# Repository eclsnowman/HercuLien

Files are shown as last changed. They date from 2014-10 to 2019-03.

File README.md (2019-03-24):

HercuLien
=========

HercuLien - Large Format, Dual Extrusion, Bowden/Direct Drive Modular, 3D Printer. Inspired by many... Created by me.

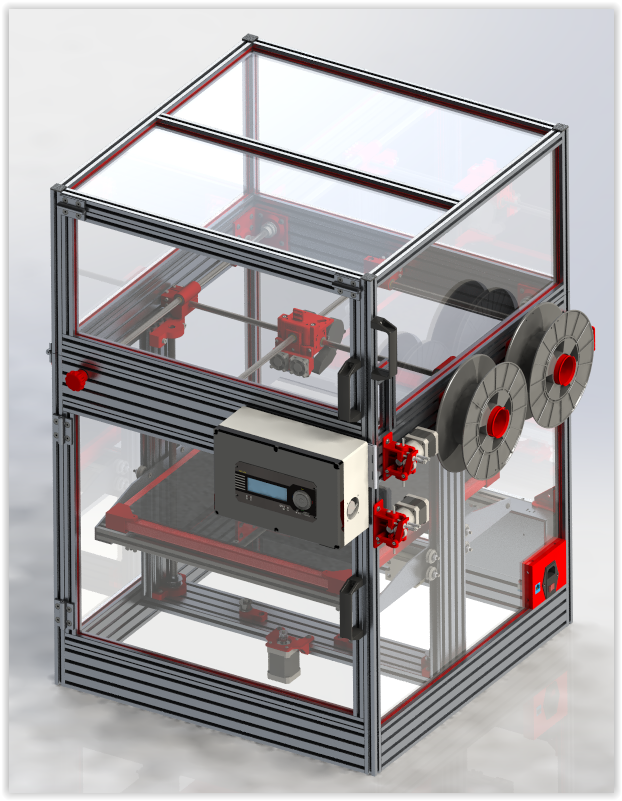
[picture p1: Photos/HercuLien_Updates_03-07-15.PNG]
HercuLien 3D Printer Render Image


This printer is the culmination of what I have learned so far since I started in 3D printing. My journey began when a friend of mine built a Prusa i3. The first time I saw his printer running I was hooked and knew I had to build one. But I was not happy with the 8"8"8" build volume of the i3. I wanted to design something bigger. At that time I had no 3D modeling experience. I figured it would be good training to learn Solidworks and design my own printer, that way once I actually built one I would have the skills to put it to use. My first attempt was my CoreXY design which is also uploaded to github. There were many things I liked about that printer, but speed and consistent print dimensions were not included in that list. 

While I was fighting with my CoreXY design I started following Tim Rastall on Google Plus. I really liked his Ingentus design, but I liked the idea of belts over spectra line. Then Jason Smith released his Eustathios designs which was a variant of of Ingentus using belts and lead screws. I knew I wanted that printer. But he released the files in sketchup. I really liked solidworks which was the software I was teaching myself during my design process. So I remodeled the Eustathios, made some changes, and eventually built the printer. The printer worked amazing. It was so much faster than my CoreY, printed part dimensions were spot on, and bowden extruders were not the nightmare I thought they would be listening to others online. In fact I designed a new extruder based on the airtripper design that allowed me to tune retraction perfectly. It is to the point that I don't think a direct drive extruder could do any better.

Once I had Eustathios up and running so well I wanted to change my CoreY to something similar. I used the aluminum frame from the CoreXY and my z-axis design which had always performed perfectly. Then I redesigned the rest from scratch. I have been running this new design for several months. I call it HercuLien (due to it's size and my last name). It is an amazing printer. I can print at very high speeds. It has a large build volume, dual extrusion, and is easily enclosed for trouble free abs printing. If you build one I hope you enjoy it as much as I have. I also hope this can act as a jumping off point for someone else to build and even better printer.

Now that Google+ has died, the Community around the HercuLien printer and the Eustathios printer have moved to: https://forum.makerforums.info/c/herculien . This is thanks in great part to Michael K Johnson, who worked his magic to retain the years of great community interaction on G+ and ported it into the Discourse community over on Makerforums. If you are looking for support or community interaction on these printers moving forward, this is the place to go.

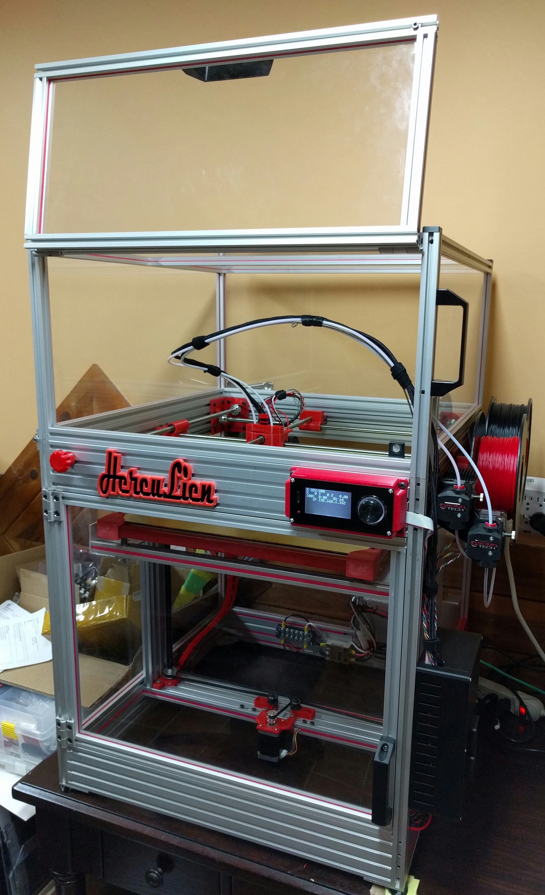
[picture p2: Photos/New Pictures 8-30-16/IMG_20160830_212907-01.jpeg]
Photo of HercuLien

(Photo of HercuLien with recent update to Azteeg X5 GT dual extruder smoothieware printer controller and Viki2 LCD)

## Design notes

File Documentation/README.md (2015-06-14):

Herculien Build Guide
=====================

This guide is intended to get you through the basics of assembling the Herculien
3D Printer.  It is a living document so be aware that the procedure is subject to change.

Pictures are included for clarity and where necessary YouTube videos will be embedded.

The guide will be structured around the subassemblies that are listed in the BOM however
to save time later we will include parts/fasteners from other subassemblies where
needed.

Tools Required
==============

 * 2.5mm Hex Wrench
 * 3mm Hex Wrench
 * Bubble Level (for leveling the Z Gantry)
 * Multimeter
 * Saw for cutting aluminum
 * Marker
 * Masking tape
 * Metric tap set (only a 5mm tap is required)
 * Drill
 * 1mm drill bit or equivalent imperial standard bit (This is just used for drilling pilot holes so it doesn't have to be precise but needs to be small enough to fit in the drill guide)
 * 5mm drill bit
 * 8mm drill bit
 * 7/8" drill bit
 * 1/2" End mill
 
Metal Preparation
=================

 1. Using the 5mm x .8 thread tap, tap all of the regular 20x80 extrusion end holes
    * Use cutting oil
    * Go Slow
    * You can either do by hand or using a drill.  If you use a drill you must take it VERY slow as you can easily break the tap bit.
 
    Example:
    How to tap an aluminum extrusion (https://www.youtube.com/watch?v=5AQUodkQZbg)

Main Frame
==========

## Parts required:

 * 9x 20x80 Aluminum Extrusions cut to 569.5mm
 * 4x 20x20 Aluminum Extrusions cut to 609.5mm
 * 2x 20x80 V-Slot Aluminum Extrusions
 * 102x T-Slot Nuts
 * 160x M5 x 10mm Button Head Screws
 * 6x M5 x 8mm Flat Head Socket Cap Screws
 * 16x M5 x 8mm Button Head Screws

## Bottom Assembly

 1. The BOM lists a 1 meter section of V-Slot, if you haven't cut the V-Slot you should do that now.
    * To cut the V-Slot you can use any saw or cutting wheel capable of cutting through a 20x80 extrusion.
    * I was successful doing this with an angle grinder and metal cutoff blade.
    * While you should be careful to cut this as straight as possible it isn't necessary to
      cut this exactly straight.  The factory cut ends are straight and those will be what is used
      to square the verticals for the Z Gantry rails to be perpendicular to the center rail.
    
 2. Using your marker and masking tape, label each of the 9 20x80 extrusions using the following labels.  These labels aren't necessary
    but will make things easier in the following steps to keep things in order.  It also helps to indicate which end it up, I use arrows
    on the masking labels.
    
    * Top Front
    * Top Rear
    * Top Right
    * Top Left
    * Bottom Front
    * Bottom Rear
    * Bottom Right
    * Bottom Left
    * Center Rail
    
    Example:
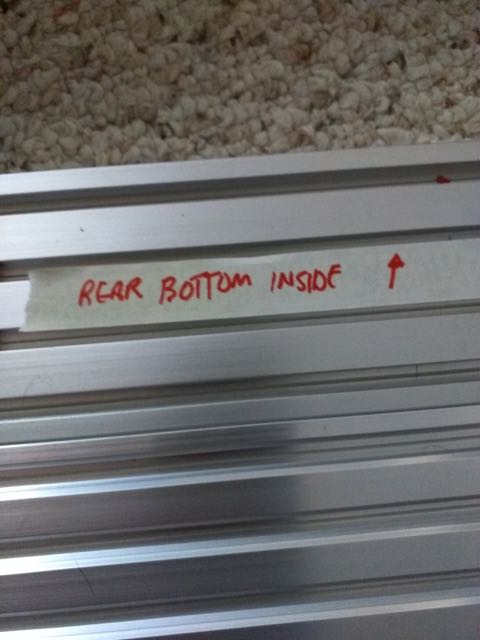
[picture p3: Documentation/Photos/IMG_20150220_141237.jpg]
20x80 Extrusion Label
    

 3. Using your marker and masking tape, label each of the 4 20x20 extrusions with the following labels.
    * Front Right
    * Rear Right
    * Front Left
    * Rear Left
    
    Example:
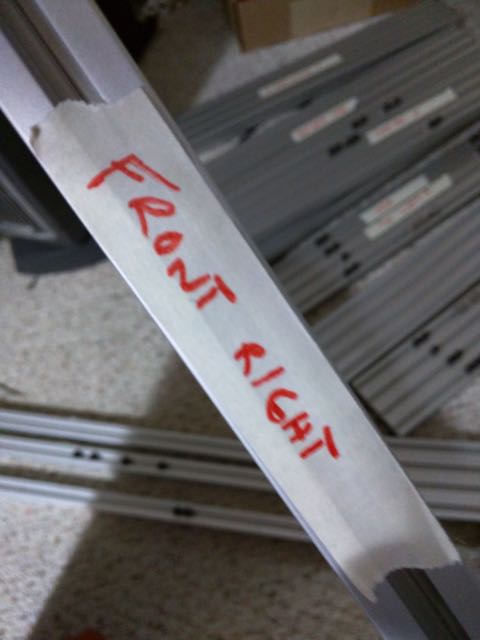
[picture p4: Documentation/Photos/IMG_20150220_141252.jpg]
20x20 Extrusion Label
    
  
 4. Locate the 4 20x20 extrusions to be used at vertical supports for the main frame.
  
 5. Using 3 M5x8mm button head screws and 2 T-Slot nuts attach the 20x20 extrusion drill guide to one end of the extrusion.
  
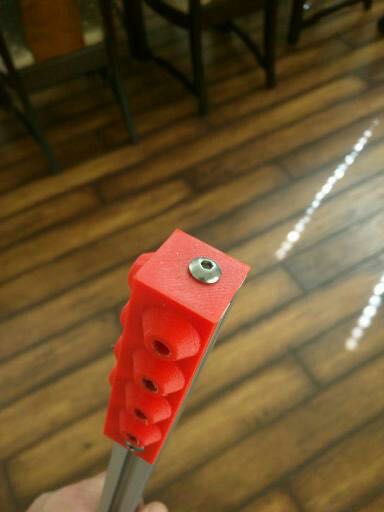
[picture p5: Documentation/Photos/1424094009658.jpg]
20x20 Extrusion Drill Guide 1
     Examples: 
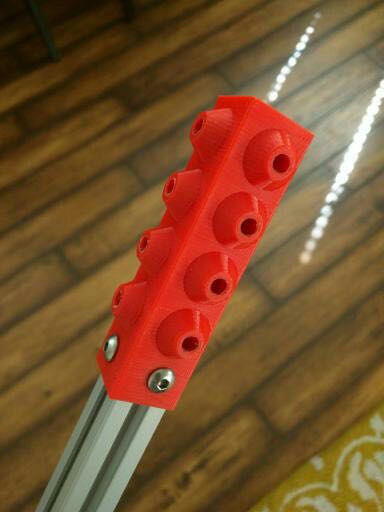
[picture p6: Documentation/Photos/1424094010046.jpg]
20x20 Extrusion Drill Guide 2
               
  
 6. Using the 5mm drill bit, drill all 8 holes using the raised drill guide holes.
     
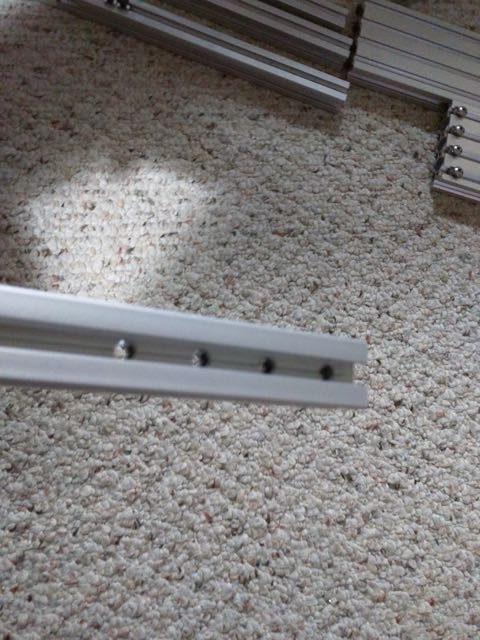
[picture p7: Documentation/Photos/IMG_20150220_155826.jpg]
20x20 Extrusion drilled
     Result: 
  
 7. Repeat this process for the other end of the extrusion and then for the remaining 3 verticals.
  
 8.  Locate the two 20x80 extrusions marked "Bottom Right" and "Bottom Left"
  
 9.  Beginning with one of these, use 4 M5x8mm button head screws and 4 T-Slot nuts attach the 20x80 8 hole drill guide but do not tighten down.
  
 10. Measure from one end of the extrusion 215mm and slide the drill guide over until the very edge of it lines up with that line.
      
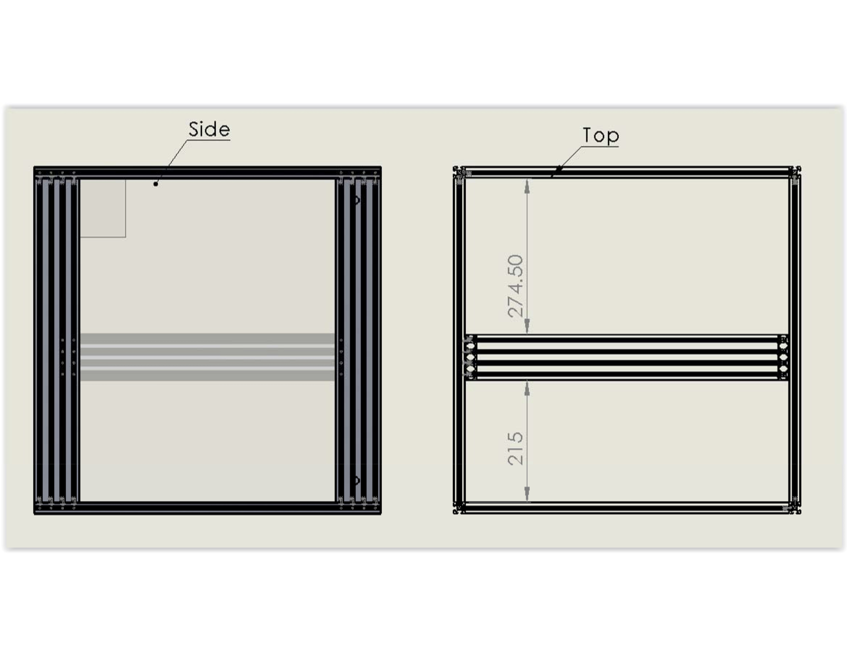
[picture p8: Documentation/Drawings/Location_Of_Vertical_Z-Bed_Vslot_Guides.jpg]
      Drawing: 
      
 11. Tighten the drill guide down and double check your measurement until it is **EXACT**
  
 12. Drill all 8 holes using the 5mm drill bit.
  
 13. Repeat for the other piece making sure your measurements are **EXACT**
  
 14. Orient the two pieces standing on their 20mm side on the floor or other flat surface keeping the perspective that you are looking at the completed chassis from the front.  e.g. "Bottom Left" goes to your left and "Bottom right" goes to your right.
  
 15. Ensure the 2 rows of holes you just drilled are nearest the top of the extrusion and the side measured 215mm from edge to the drill guide is placed facing you.
  
 16. Now using the masking tape and markers label the inside face of each so that the orientation is clear.
      
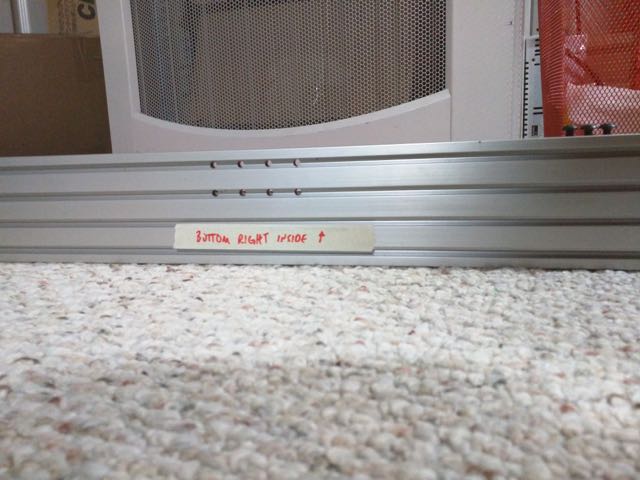
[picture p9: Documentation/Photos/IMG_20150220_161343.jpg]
20x80mm Extrusion Bottom Right
      Result: 
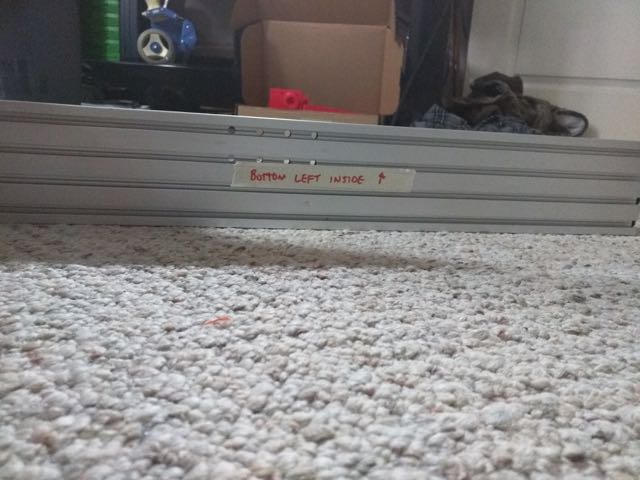
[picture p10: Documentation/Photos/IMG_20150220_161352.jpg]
20x80mm Extrusion Bottom Left
              
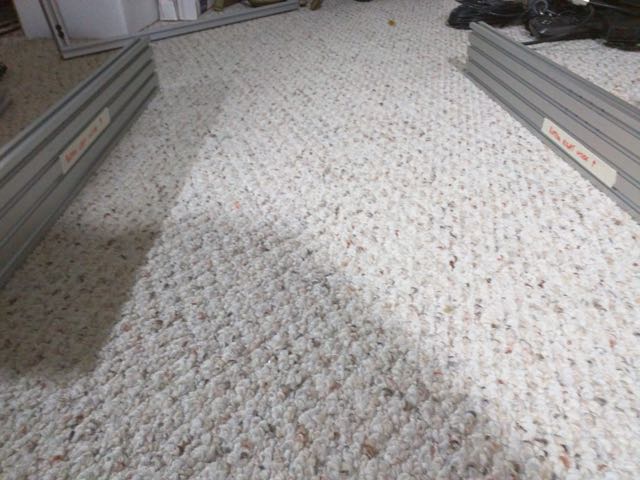
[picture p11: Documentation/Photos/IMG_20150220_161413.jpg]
20x80mm Extrusions properly oriented
              
   
 17. Locate the 20x80 extrusion pieces marked "Bottom Front" and "Bottom Rear"
 
 18. Orient the pieces on the floor or flat surface with the 2 bottom left and right extrusions with one 20mm side lying flat on the surface.
 
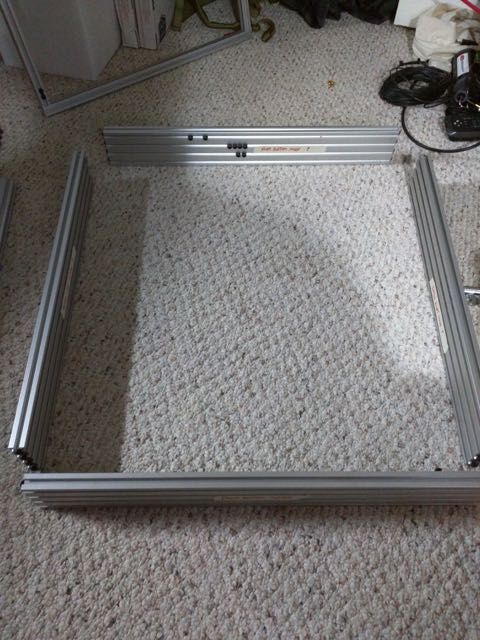
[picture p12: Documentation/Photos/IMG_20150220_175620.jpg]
20x80mm Extrusions oriented correctly
     Example: 
 
 19. Using the marker and masking tape, label the inside of each and use an drawn arrow to indicate which way is up.
 
 20. On the piece marked "Bottom Rear" insert 2 T-Slot nuts in the top row of the innermost side.  Insert 4 T-Slot nuts in the row below that.  Insert 2 T-Slot nuts in the row below that.  Use M5x10mm button head screws hand tightened to hold them in place.
 
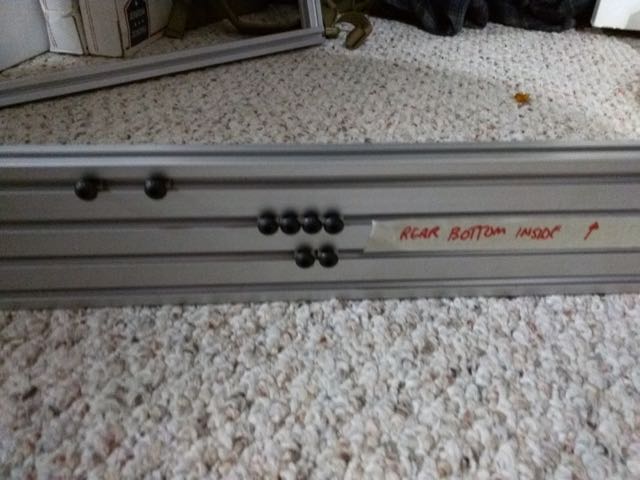
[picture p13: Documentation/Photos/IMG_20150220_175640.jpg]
Bottom Rear Extrusion Nuts Installed
     Example: 

 21. On the piece marked "Bottom Front" insert 1 T-Slot nut on the top row of the innermost side.  Insert 1 T-Slot nut in the row below that.  Use M5x10mm button head screws, hand tightened, to hole them in place.
 
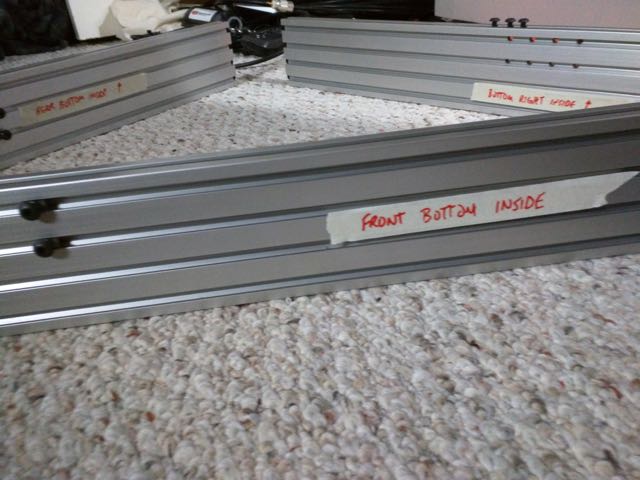
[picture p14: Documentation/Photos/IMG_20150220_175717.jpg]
Bottom Front Extrusion Nuts Installed
     Example: 
 
 22. On the piece marked "Bottom Right" insert 3 T-Slot nuts on the top row and use M5x10mm button top screws, hand tightened, to hold them in place.
     
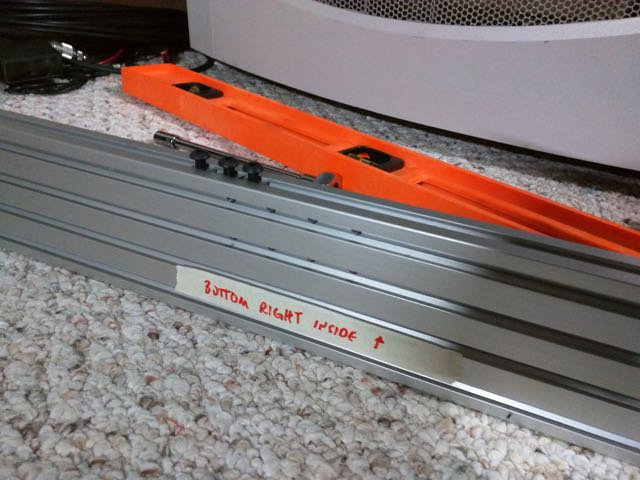
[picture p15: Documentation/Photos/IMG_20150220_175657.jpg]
Bottom Right Extrusion Nuts installed
     Example: 
 
 23. Thread M5x10mm button head screws into each of the 4 holes on each end of the 4 bottom 20x80mm extrusions placed on the flat surface from earlier.  Thread the screws in until there is only approximately 3-4mm of thread showing.
 
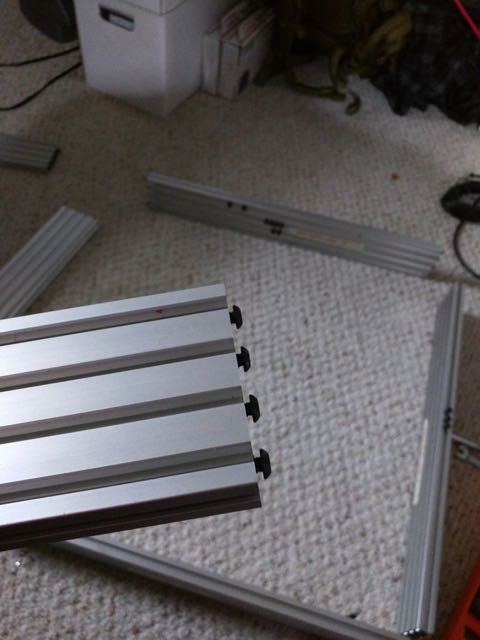
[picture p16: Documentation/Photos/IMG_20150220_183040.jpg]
Extrusion end screws installed
     Example: 
 
 24. Locate the 20x80 extrusion labeled "Center Rail"
 
 25. Thread M5x10mm button head screws in the 4 holes in each of the ends of the "Center Rail" leaving only about 3-4mm of thread showing.
 
 26. Slide one side of the center rails button head screws in the bottom left 20x80 extrusion's second from the top slot and visually line it up with the 4 holes that are drilled in the bottom left piece.
     
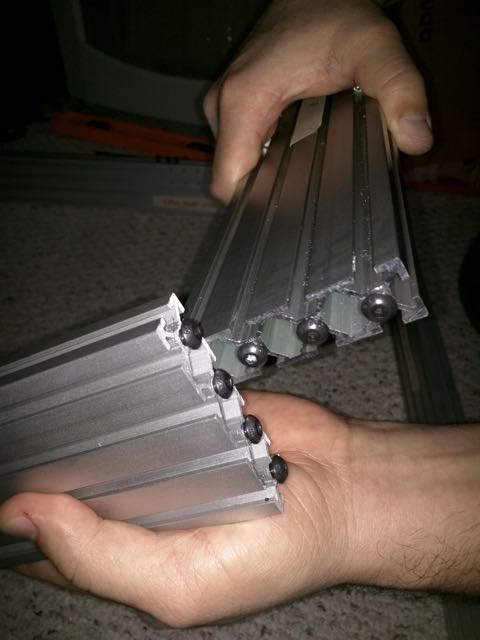
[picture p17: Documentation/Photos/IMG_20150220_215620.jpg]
Attaching Center Rail to Bottom Left extrusion
     Example: 
     
 27. Using your measuring tool measure 215mm from the front edge of the "Bottom Left" 20x80mm extrusion to the edge of the "Center Rail".
     
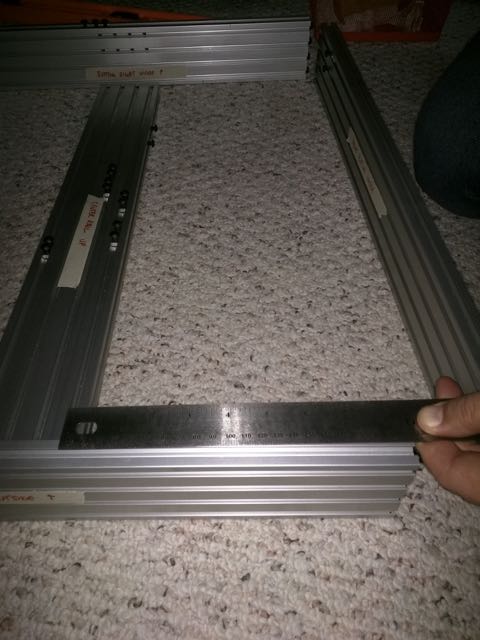
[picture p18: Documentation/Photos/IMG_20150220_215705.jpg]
Measuing Center Rail Placement
     Example: 
 
 28. Passing the 2.5mm hex wrench through the holes in the opposite side of the "Front Left" extrusion tighten the button head screws on the "Center Rail" locking them in place.  Be sure to double check your measurements.
 
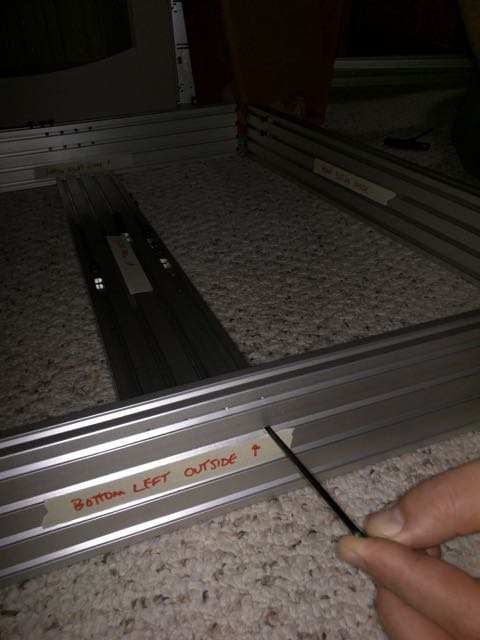
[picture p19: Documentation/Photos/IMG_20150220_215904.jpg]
Tightening the Center Rail
     Example: 
 
 29. The Front of the Center rail is now the side measured 215mm away from the front edge of the supporting extrusion.  If it helps you to keep track of these things use the masking tape and marker to label the side that is front.
 
 30. On the front side of the center rail insert 2 T-Slot nuts and use 2 M5x10mm button head screws, hand tightened, to hold them in place. On the top of the "Center Rail" in the first of four slots insert 4 T-Slot nuts with M5x10mm button head screws to hold them in place.  Do the same for the second from the front edge slot.  Skip the third slot and on the foourth slot from the front insert 2 T-Slot Nuts with 2 M5x10mm button head screws to hole them in place.
     
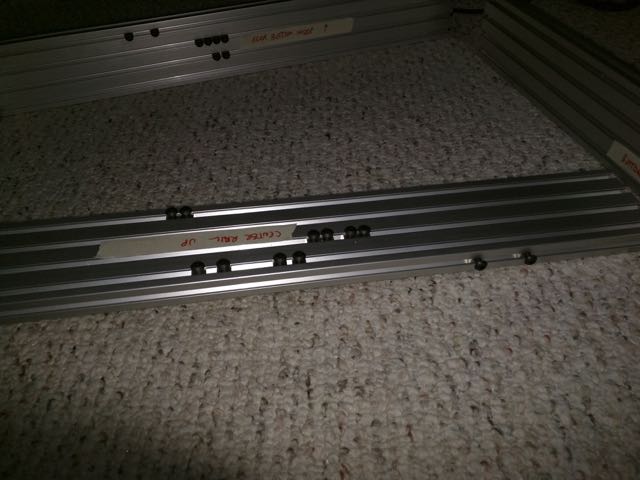
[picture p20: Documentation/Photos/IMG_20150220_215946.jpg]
Setup T-Slot nuts for later mounting things
     Example: 
     
 31. Now repeat step 26-28 for the other side of the Center Rail, securing the Center Rail to the "Bottom Right" 20x80mm extrusion.
 
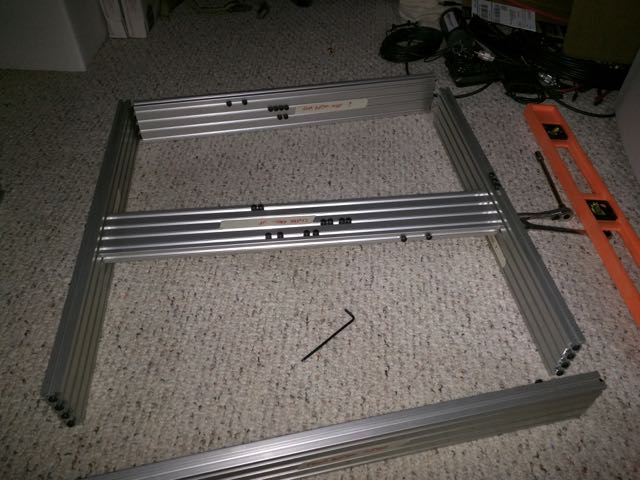
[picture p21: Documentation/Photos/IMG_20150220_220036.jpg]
Finished Center Rail
     Example: 
 
 32. Locate the 2 V-Slot 20x80 extrusions measuring 489.5mm.  These do not need labels as they are identical and either will work on either side.
 
 33. With one of the V-Slot extrusions on one 80mm side nearest the factory straight cut insert 1 T-Slot nut in each slot and hand thread 1 M5x8mm button head screw for each T-Slot nut but do not tighten.
 
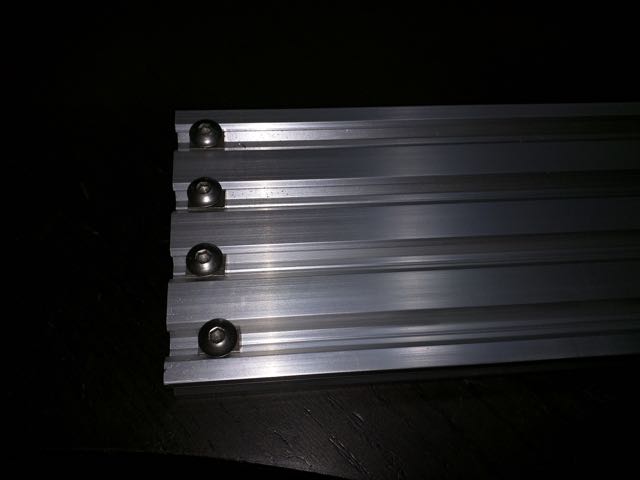
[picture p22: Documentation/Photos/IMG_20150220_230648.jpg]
V-Slot extrusion with T-Slot nuts prepped
     Example: 
 
 34. Slide the button head screws in the top slot of the "Bottom Left" 20x80mm extrusion.  I find it's easier to stand the "Bottom Left", "Center Rail" and "Bottom Right" assembled pieces on one end so that it looks like an "H".
 
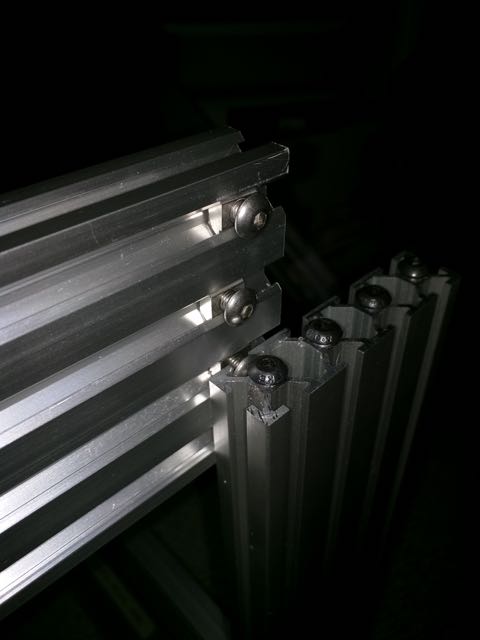
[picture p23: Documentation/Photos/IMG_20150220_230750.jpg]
Inserting V-Slot button head screws into 20x80mm T-Slot extrusion
     Example: 
 
 35. Carefully slide this assembly down the rail and place it sitting on top of the Center Rail extrusion and make sure the edges of the V-Slot are flush with the Center Rail extrusion on both sides.
 
 36. Passing the 2.5mm hex wrench through the holes on the opposite side of the "Bottom Left" extrusion tighten down each screw.
 
 37. Double check your measurements and ensure that the front 20mm edge of the V-Slot extrusion is exactly 215mm away from the front edge of the "Bottom Left" extrusion.
 
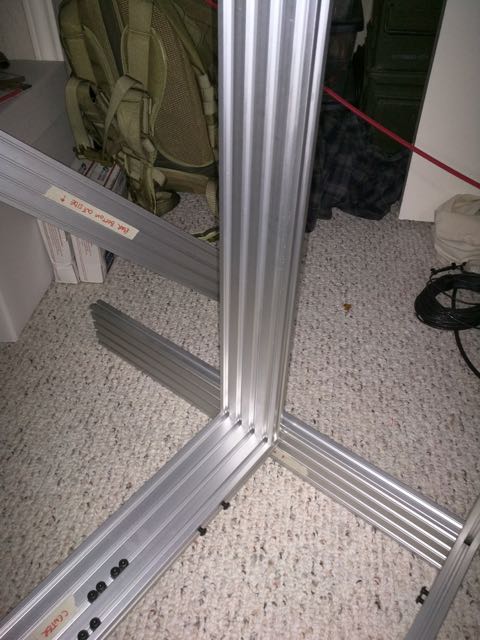
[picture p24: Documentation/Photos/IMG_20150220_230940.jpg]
V-Slot vertical in place
     Example: 
 
 38. Repeat steps 33-37 for the "Bottom Right" 20x80mm extrusion using the remaining V-Slot extrusion.
 
 39. Locate the 4 20x20 extrusions that are 609.5mm long.  These are the verticals to hold everything upright.
 
 40. Find the 20x80 extrusions marked "Bottom Front" and "Bottom Left" and use the 20x20 vertical marked "Front Left" for the next step.
     
 41. Slide button head screws at the end of the "Bottom Front" 20x80 extrusion's left side into the slot of the 20x20mm extrusion and then do the same with the 20x80mm "Bottom Left" extrusion at a right angle to the "Bottom Front" extrusion.  See picture for example.
     
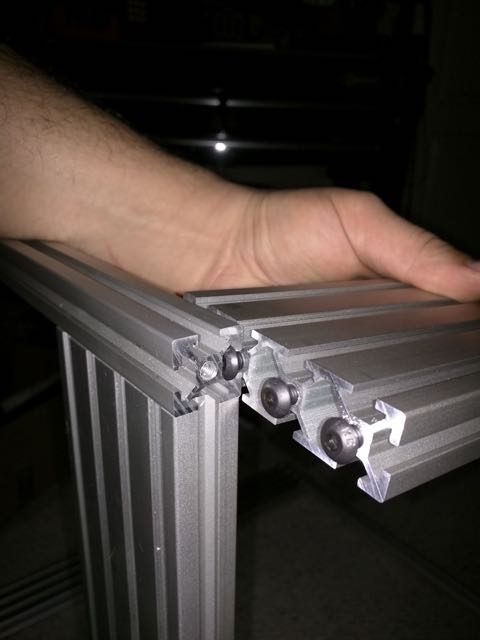
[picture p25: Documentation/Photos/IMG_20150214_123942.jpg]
Building a corner
     Example: 
 
 42. Use your 2.5mm hex wrench to tighten the button head screws by passing the wrench through the holes drilled in the 20x20 extrusion.  **ENSURE** the bottom of the 20x80 extrusions are flush with the bottom of the vertical 20x20 extrusion.
     
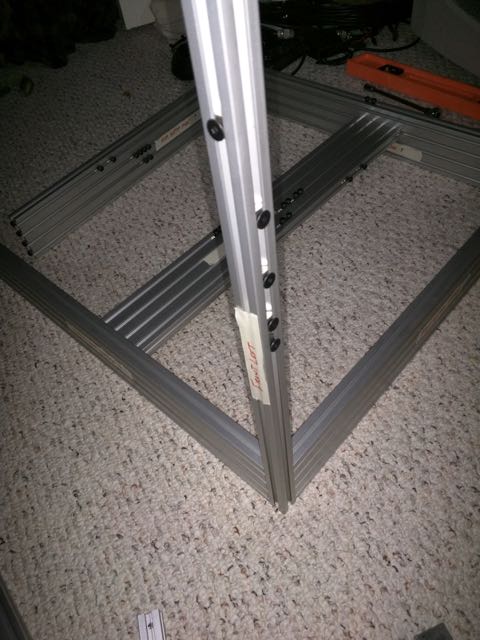
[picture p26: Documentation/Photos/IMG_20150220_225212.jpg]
Corner Vertical installed
     Example: 
     
 43. Repeat steps 25-27 for the 4 corners paying close attention to use the correct vertical per corner.  If you use the wrong one, you can switch their labels once you're finished.  The labeling matters in the coming steps.
     
     Example: All corners done, bottom assembly complete
 
## Top Assembly

 1. Locate the 20x80mm extrusion marked "Top Front" and lay it flat on one of it's 80mm sides in front of you.
 
 2. We will assume this is now the inside of the top front extrusion and the 20mm side furthest from you is the side that will be at the top of the finished chassis., mark it with the tape and marker.
    
    Example: Top Front extrusion properly labeled
    
 3. Locate Corner Bearing Bracket B, this is a printed part.
 
 4. Place Corner Bearing Bracket B on the right side of the 80mm side facing you with the bearing support hole closest to the edge of the printed part laying flat on the extrusion.  Make sure the printed part is lined up against the right edge with the opposing bearing support hole vertical and flush with the edge.
 
    Example: Corner Bearing Bracket B placed properly on extrusion
 
 5. Locate the printed extrusion drill guide shown below.
 
    Example: Pilot hole drill guide
 
 6. Place this drill guide under the Corner Bearing bracket and make note of the hole you should be drilling, it will be in the center of the hole in the corner bearing bracket.  It should be the top most pilot hole on the drill guide.
 
    Example: Drill guide placed under bearing bracket
             Drill this hole
 
 7. Set the Corner Bearing Bracket B aside for later use.
 
 8. Using 4 M5x10mm button head screws secure the drill guide to the right edge of the extrusion.
 
    Example: Screws in the 4 holes on this side
 
 9. Using 2 T-Slot nuts and 2 M5x10mm button head Screws secure the 2 holes on the upper face of the drill guide to the extrusion.
 
    Example: Secure these holes
 
 10. If you have access to a drill press you would be best served using it for the next drilling steps but a hand drill used carefully will suffice.
 
 11. Drill the top most pilot hole using a small bit.
 
 12. Remove the drill guide and set the screws and T-Slot nuts aside.
 
 13. Using a slightly larger bit (I used a 5mm bit) drill out the pilot hole.
 
 14. Using your 1/2" end mill drill the final hole through the extrusion.
 
     Example: Finished 1/2 inch hole
 
 15. At this time you can choose to use a round file to clean up the drilled hole.
 
 16. Lay the extrusion down on a table or the floor in front of you with the labeled inside facing you and the top 20mm side facing away from you.
 
     Example: Orient the extrusion correctly
 
 17. In the slot closest you insert 8 T-Slot nuts and hand tighten 1 M5x10mm button head screw into each so that the T-Slot nuts do not slide around.
 
 18. In the slot above that insert 4 T-Slot nuts and hand tighten 1 M5x10mm button head screw into each so that the T-Slot nuts do not slide around.
 
 19. In the slot above that insert 2 T-Slot nuts and hand tighten 1 M5x10mm button head screw into each so that the T-Slot nuts do not slide around.
 
 20. In the top slot insert 4 T-Slot nuts and hand tighten 1 M5x10mm button head screw into each so that the T-Slot nuts do not slide around.

     Example: Inserted T-Slot nuts
 
 21. Thread M5x10mm button head screws into the 4 holes on each end of the extrusion.
 
     Example: Ends threaded
 
 22. Set this extrusion aside for later use.
 
 23. Locate the 20x80mm extrusion labeled "Top Rear" and lay it flat on one of it's 80mm sides in front of you.
 
 24. We will assume this is now the inside of the top rear extrusion and the 20mm side furthest from you is the side that will be at the top of the finished chassis., mark it with the tape and marker.
 
     Example: Top Rear properly labeled
 
 25. Locate Corner Bearing Bracket B, this is a printed part.
 
 26. Place Corner Bearing Bracket B on the right side of the 80mm side facing you with the bearing support hole closest to the edge of the printed part laying flat on the extrusion.  Make sure the printed part is lined up against the right edge with the opposing bearing support hole vertical and flush with the edge.
 
     Example: Corner Bearing Bracket B placed properly on extrusion
     
 27. Locate the printed extrusion drill guide shown below.
 
     Example: Pilot hole drill guide
 
 28. Place this drill guide under the Corner Bearing bracket and make note of the hole you should be drilling, it will be in the center of the hole in the corner bearing bracket.  It should be the top most pilot hole on the drill guide.
     
     Example: Drill guide placed under bearing bracket
             Drill this hole
     
 29. Set the Corner Bearing Bracket B aside for later use.
 
 30. Using 4 M5x10mm button head screws secure the drill guide to the right edge of the extrusion.
 
    Example: Screws in the 4 holes on this side
 
 31. Using 2 T-Slot nuts and 2 M5x10mm button head Screws secure the 2 holes on the upper face of the drill guide to the extrusion.
 
    Example: Secure these holes
 
 32. If you have access to a drill press you would be best served using it for the next drilling steps but a hand drill used carefully will suffice.
 
 33. Drill the top most pilot hole using a small bit.
 
 34. Remove the drill guide and set the screws and T-Slot nuts aside.
 
 35. Using a slightly larger bit (I used a 5mm bit) drill out the pilot hole.
 
 36. Using your 1/2" end mill drill the final hole through the extrusion.
 
     Example: Finished 1/2 inch hole
 
 37. At this time you can choose to use a round file to clean up the drilled hole.
 
 38. Lay the extrusion down on a table or the floor in front of you with the labeled inside facing you and the top 20mm side facing away from you.
 
     Example: Orient the extrusion correctly
 
 39. In the slot closest you insert 4 T-Slot nuts and hand tighten 1 M5x10mm button head screw into each so that the T-Slot nuts do not slide around.
 
 40. In the slot above that insert 4 T-Slot nuts and hand tighten 1 M5x10mm button head screw into each so that the T-Slot nuts do not slide around.
 
 41. In the slot above that insert 2 T-Slot nuts and hand tighten 1 M5x10mm button head screw into each so that the T-Slot nuts do not slide around.
 
 42. In the top slot insert 4 T-Slot nuts and hand tighten 1 M5x10mm button head screw into each so that the T-Slot nuts do not slide around.

     Example: T-Slot nuts properly installed
 
 43. Thread M5x10mm button head screws into the 4 holes on each end of the extrusion.
 
     Example: Ends threaded
 
 44. Set this extrusion aside for later use.
 
 45. Find the 20x80mm extrusion labeled "Top Left" and lay it flat on one of it's 80mm sides in front of you.
 
 46. We will assume this is now the inside of the top rear extrusion and the 20mm side furthest from you is the side that will be at the top of the finished chassis., mark it with the tape and marker.
 
     Example: Top Left properly labeled
  
 47. Locate Corner Bearing Bracket A, this is a printed part.
 
 48. Place Corner Bearing Bracket A on the right side of the 80mm side facing you with the bearing support hole closest to the edge of the printed part laying flat on the extrusion.  Make sure the printed part is lined up against the right edge with the opposing bearing support hole vertical and flush with the edge.
 
     Example: Corner Bearing Bracket A placed correctly
     
 49. Locate the printed extrusion drill guide shown below.
 
     Example: Pilot hole drill guide
 
 50. Place this drill guide under the Corner Bearing bracket and make note of the hole you should be drilling, it will be in the center of the hole in the corner bearing bracket.  It should be the second pilot hole from the bottom on the drill guide.
     
     Example: Drill guide placed correctly
              Drill this hole
     
 51. Set the Corner Bearing Bracket A aside for later use.
 
 52. Using 4 M5x10mm button head screws secure the drill guide to the right edge of the extrusion.
 
    Example: Screws in the 4 holes on this side
 
 53. Using 2 T-Slot nuts and 2 M5x10mm button head Screws secure the 2 holes on the upper face of the drill guide to the extrusion.
 
    Example: Secure these holes
 
 54. If you have access to a drill press you would be best served using it for the next drilling steps but a hand drill used carefully will suffice.
 
 55. Drill the top most pilot hole using a small bit.
 
 56. Remove the drill guide and set the screws and T-Slot nuts aside.
 
 57. Using a slightly larger bit (I used a 5mm bit) drill out the pilot hole.
 
 58. Using your 1/2" end mill drill the final hole through the extrusion.
 
     Example: 1/2 inc hole drilled
 
 59. At this time you can choose to use a round file to clean up the drilled hole.
 
 60. Locate Corner Bearing Bracket B, this is a printed part.
 
 61. Place Corner Bearing Bracket B on the left side of the 80mm side facing you with the bearing support hole closest to the edge of the printed part laying flat on the extrusion.  Make sure the printed part is lined up against the right edge with the opposing bearing support hole vertical and flush with the edge.
 
     Example: Corner Bearing Bracket B placed correctly
     
 62. Locate the printed extrusion drill guide shown below.
 
     Example: Pilot hole drill guide
 
 63. Place this drill guide under the Corner Bearing bracket and make note of the hole you should be drilling, it will be in the center of the hole in the corner bearing bracket.  It should be the second pilot hole from the bottom on the drill guide.
     
     Example: Drill guide placed under the bearing bracket
              Drill this hole
     
 64. Set the Corner Bearing Bracket B aside for later use.
 
 65. Using 4 M5x10mm button head screws secure the drill guide to the right edge of the extrusion.
 
    Example: Screws in the 4 holes on the side
 
 66. Using 2 T-Slot nuts and 2 M5x10mm button head Screws secure the 2 holes on the upper face of the drill guide to the extrusion.
 
    Example: Secure these holes
 
 67. If you have access to a drill press you would be best served using it for the next drilling steps but a hand drill used carefully will suffice.
 
 68. Drill the top most pilot hole using a small bit.
 
 69. Remove the drill guide and set the screws and T-Slot nuts aside.
 
 70. Using a slightly larger bit (I used a 5mm bit) drill out the pilot hole.
 
 71. Using your 1/2" end mill drill the final hole through the extrusion.
 
     Example: 1/2 inch hole drilled
 
 72. Locate the drill guide shown below
 
     Example: V-Slot support drill guide
 
 73. With the 20x80mm Top Left extrusion sitting on the table in front of you with the inside side facing up and the 20mm side labeled as the top of the extrusion facing away from you place the drill guide on the bottom edge as shown.
 
     Example: Drill guide placed this way
 
 74. Measure **exactly** 215mm from the left edge of the extrusion  and slide the edge of the drill guide to that point.
 
     Example: Measuring 215mm to edge of the drill guide
 
 75. Using 4 T-Slot nuts and 1 M5x8mm button head screw per nut secure the drill guide holes on this side taking special care to preserve the 215mm from the left edge.
 
     Example: Secure these holes
 
 76. You can optionally secure 2 to 4 of the holes on the top side of the drill guide but I've found that it isn't 100% necessary, I did this both ways and the result came out the same.
 
 77. Drill these 4 holes with a 5mm drill bit.
 
     Example: Drill these holes
              Holes drilled
 
 78. Place the 20x80mm Top Left extrusion sitting on the table in front of you with the inside side facing up and the 20mm side labeled as the top of the extrusion facing away from you.
 
 79. Locate 4 T-Slot Nuts and 4 M5x8mm button head screws.
 
 80. Thread the 8mm screws into the T-Slot nuts as shown below.
 
     Example: 8mm screws and T-Slot nuts
 
 81. In the slot of the extrusion closest to you slide the 4 button head screw tops in like this.
 
     Example: Center support screws inserted
 
 82. On each side of these 4 screws insert 2 T-slot nuts and secure them with 1 M5x10mm button head screw each, hand tightened to keep them from sliding.
 
 83. In the slot above this insert 2 T-Slot nuts and secure them with 1 M5x10mm button head screw each, hand tightened to keep them from sliding.
 
 84. In the slot above this insert 4 T-Slot nuts and secure them with 1 M5x10mm button head screw each, hand tightened to keep them from sliding.
 
 85. In the top most slot insert 4 T-Slot nuts and secure them with 1 M5x10mm button head screw each, hand tightened to keep them from sliding.
 
 86. Thread M5x10mm button head screws into the 4 holes on each end of the extrusion.
 
     Example: Ends threaded
 
 87. The end result should look like this.
 
     Example: Top Left 20x80mm extrusion finished
 
 88. Set this extrusion aside for later use.
 
 89. Locate the 20x80mm extrusion marked "Top Right" and lay it flat on one of it's 80mm sides in front of you.
 
 90. We will assume this is now the inside of the top rear extrusion and the 20mm side furthest from you is the side that will be at the top of the finished chassis., mark it with the tape and marker.
 
     Example: Top Right properly labeled
 
 91. Locate the drill guide shown below
 
     Example: V-Slot support drill guide
 
 92. With the 20x80mm Top Right extrusion sitting on the table in front of you with the inside side facing up and the 20mm side labeled as the top of the extrusion facing away from you place the drill guide on the bottom edge as shown.
 
     Example: Drill guide placed this way
 
 93. Measure **exactly** 215mm from the right edge of the extrusion and slide the edge of the drill guide to that point.
 
     Example: Measuring 215mm to edge of the drill guide
 
 94. Using 4 T-Slot nuts and 1 M5x8mm button head screw per nut secure the drill guide holes on this side taking special care to preserve the 215mm from the left edge.
 
     Example: Secure these holes
 
 95. You can optionally secure 2 to 4 of the holes on the top side of the drill guide but I've found that it isn't 100% necessary, I did this both ways and the result came out the same.
 
 96. Drill these 4 holes with a 5mm drill bit.
 
     Example: Drill these holes
              Holes drilled
 
 97. Place the 20x80mm Top Left extrusion sitting on the table in front of you with the inside side facing up and the 20mm side labeled as the top of the extrusion facing away from you.
 
 98. Locate 4 T-Slot Nuts and 4 M5x8mm button head screws.
 
 99. Thread the 8mm screws into the T-Slot nuts as shown below.
 
     Example: 8mm screws and T-Slot nuts
 
 100. In the slot of the extrusion closest to you slide the 4 button head screw tops in like this.
 
     Example: Center support screws inserted
 
 101. On each side of these 4 screws insert 2 T-slot nuts and secure them with 1 M5x10mm button head screw each, hand tightened to keep them from sliding.
 
 102. In the slot above this insert 2 T-Slot nuts and secure them with 1 M5x10mm button head screw each, hand tightened to keep them from sliding.
 
 103. In the slot above this insert 4 T-Slot nuts and secure them with 1 M5x10mm button head screw each, hand tightened to keep them from sliding.
 
 104. In the top most slot insert 6 T-Slot nuts and secure them with 1 M5x10mm button head screw each, hand tightened to keep them from sliding.
 
 105. The end result should look like this.
 
     Example: Top Right 20x80mm extrusion finished
 
 106. Flip the extrusion over so that the outside side is facing up.
 
      Example: Top Right outside labeled correctly
 
 107. In the slot closest to you, the bottom most slot, insert 5 T-Slot nuts and secure them with 1 M5x10mm button head screw each, hand tightened to keep them from sliding.
 
 108. In the top most slot on the outer side insert 5 T-Slot nuts and secure them with 1 M5x10mm button head screw each, hand tightened to keep them from sliding.
 
 109. Thread M5x10mm button head screws into the 4 holes on each end of the extrusion.
 
     Example: Ends threaded
 
 110. The end result should look like this.
 
      Example: T-Slot nuts setup on outside of Top Rear
 
 110. Set this extrusion aside for later use.

## Power supply and switch plate

 1. Locate the printed part "Outlet Switch and Network Mount" and the Electrical fused plug part ordered from the BOM.
 
    Example: Outlet Switch and Network Mount printed part
 
 2. Slide the fused plug into the outlet switch and network mount printed part.
 
    Example: Fused plug goes in this hole... obviously.
 
 3. Mark the hole on either side of the fused plug for drilling and remove the fused plug from the printed part.
 
 4. Using a 3mm or equivalent drill bit, drill the 2 holes.
 
 5. Slide the fused plug back into the outlet switch and network mount plate and line up the holes in the fused plug with the drilled holes.
 
 6. Using an M3x12mm socket cap screw and an M3 lock nut secure the fused switch to the printed part for each hole.
 
    Example: Fused plug secured in outlet switch mount
 
 7. On the "Bottom Right" 20x80mm extrusion remove 2 of the M5x10mm button head screws from the 2 T-slot nuts closest to the right rear corner.
 
 8. Slide all T-Slot nuts out of the way of the rear corner to make it easier to slide them into place later.
 
 9. With the outlet switch printed part laying down on a flat surface with the switch side up, locate the 2 holes on the right side.
 
    Example: These holes
 
 10. Insert 1 M5x8mm button head screw in each hole from the inside.
 
     Example: Screws here.
 
 11. Thread 1 T-Slot nut on each screw to prepare the switch for securing into the rear right corner 20x20mm vertical extrusion.
 
     Example: T-Slot nuts threaded properly
 
 12. Slide the T-Slot nuts in the rear right vertical extrusion on the face that is facing the front of the chassis.
 
     Example: Slide nuts into the rear right vertical extrusion.
 
 13. Slide the printed part all the way down to the bottom and secure the 2 button head screws from the inside.
 
 14. Using a long hex wrench slide 1 T-Slot nut under the outlet switch and network mount printed part until it lines up with the rear most hole.
 
 15. Use 1 M5x8mm button head screw to secure this T-Slot nut.
 
 16. Repeat steps 14-15 for the other bottom hole of the outlet switch mount.
 
     Example: Fused plug and outlet switch plate mounted.
 
 17. Locate the power supply and 3 printed power supply brackets.
 
     Example: Power supply mounting brackets
 
 18. Place the power supply laying flat on a surface in front of you with the fan side down and the terminal side facing left.
 
 19. Using an M4x10mm screw secure the side of the 2 identical printed brackets to the bottom side of the power supply. This will be the side facing you.
 
     Example: Brackets mounted
 
 20. In the remaining power supply bracket insert 1 M5x8mm button head screw into each of the 2 holes on the extrusion mount side. Thread a T-Slot nut on each screw.
 
     Example: Screws inserted into the bracket
 
 21. On the side of the power supply facing away from you, top side, use an M4x8mm screw to secure the remaining printed bracket to the power supply.
 
     Example: Bracket installed
 
 22. Begin installing the power supply by sliding the 2 threaded T-Slot nuts into the rear right vertical extrusion on the left side of the extrusion.
 
     Example: Installing the power supply
              Power supply slid down to the back right corner
 
 23. Now is a great time to check the input voltage.  For the US set the switch to 115V.
 
     Example: Setting the voltage
 
 24. Using the T-Slot nuts installed in the front face of the rear bottom extrusion secure the remaining power supply brackets.
 
     Example: Power supply secured
 
## Z-Gantry

 Parts needed:
    * 8 Openbuilds V-Slot wheel kits
    * 8 1/4" eccentric spacers
    * 8 M5x25mm button head screws
    * 8 M5 15mm OD washer
    * 2 Delrin lead screw nuts (See BOM for part number)
    * 2 12mm lead screws (See BOM for part number")
    * 4 608ZZ bearings
    * 4 8mm shim washers
    * 4 M5x25mm socket head cap screws
    * 4 M5x16mm button head socket cap screws
    * 2 36 tooth pulleys
    * 2 Z Leadscrew top bearing holders
    * 2 Z Leadscrew bottom bearing holders
    * 8 M5x8mm button head screws
    * 4 M5x10mm button head screws

 1. Locate the 2 Z-Gantry angle plates.
 
 2. Using the drawings below, make the necessary cuts and holes to both Z-Gantry Plates.
 
    Drawings: Wheel Face
              Bottom side
 
 3. This would be a great time to paint the plates if you want to.
 
    Example: Painted Z-Gantry Plate
 
 4. Set one plate aside.
 
 5. With one Z gantry angle plate drilled and prepped (optionally painted) locate 1 M5x25mm button head screw, 1 V-Slot wheel kit 1 M5 15mm OD washer and 1 1/4" eccentric spacer.
 
 6. Assemble the wheel assembly as shown below.
 
    Assembly: Step 1
              Step 2
              Step 3
              Step 4
              Step 5
 
 7. Tighten down the wheel assembly on the z gantry plate until it's snug but still can be adjusted with a box end wrench.
    
 8. Repeat this process for all 4 wheel mounting holes but before tightening down one of the top wheels insert the printed Z end stop tab. Pay attention to which wheel you are putting this on to be sure you want your Z end stop mounted on that side of the Z uprights..
 
    Example: Z Endstop tab
 
 9. Using a bubble level and a box end wrench that fits your eccentric spacer balance the Z gantry plate.  This can take quite a while so be patient and make sure things are level.
 
    Example: Example 1
             Example 2
             Example 3
             Example 4
 
 10. Repeat steps 5 through 9 for the other gantry plate.
 
 11. Locate the 2 20x20mm extrusions measuring 519.5mm in length.
 
     Example: Extrusions
 
 12. Tap each of the end holes on these 2 extrusions using your M5 x .8mm thread tap.
 
 13. Set one extrusion aside for later.
 
 14. Locate 1 M5x10mm button head screw and 1 oversized M5 washer (15mm OD)
 
 15. Line an extrusion up with the single hole at the end of one of the Z gantry plates and thread the screw through the washer, then the gantry plate hole and finally into the end of the 20x20mm extrusion.
 
     Example: Extrusion snugged down
 
 16. Tighten but only until slightly snug.
 
 17. Insert 2 T-Slot nuts in the bottom slot of the extrusion
 
     Example: T-Slot nuts
 
 18. Line these up with the 2 holes in the bottom of the z gantry plate.
 
 19. Thread 1 M5x8mm button head screw through an M5 washer (not oversized)
 
 20. Insert this screw into one of the holes on the bottom of the z gantry plate and into the T-Slot nut.  Snug the connection down but not tight.
 
     Example: Bottom of extrusion secured
 
 21. Repeat steps 19-20 for the other hole in the Z gantry plate on that side.
 
 22. Repeat steps 14 - 21 for the other side of the gantry plate.
 
 23. Insert 2 more T-Slot nuts in the bottom of each 20x20mm extrusion for the other gantry plate.
 
 24. Repeat steps 14-22 for the other gantry plate.
 
 25. Tighten down all of the screws to complete the Z gantry plate/extrusion assembly.
 
     Example: Z-Gantry example 1
              Z-Gantry example 2
 
 26. Locate 1 Delrin leadscrew nut, 2 M5x16mm button head screws, 2 M5 lock nuts and 4 M5 standard washers.
 
     Example: Leadscrew hardware
 
 27. Place 1 washer on each button head screw and feed each screw through a small hole in the center of one of the gantry plates.
 
     Example: Gantry screws in place
              Gantry screws in place
 
 28. Feed the long end of the delrin nut through the gantry plate's big hole between the 2 screws aligned with the screws and seat it firmly.
 
     Example: Delrin nut in place
 
 29. Using the remaining 2 washers and lock nuts secure the delrin leadscrew nut but do not tighten things down yet.
 
     Example: Secured
 
 30. Repeat steps 27-29 for the other Z-Gantry plate.
 
 31. Print the heat spreader template and tape it together taking care to make sure the lines are aligned properly.  Make sure you print it raw and do not fit to page.
 
     Template: [Heat Spreader Template](./Templates/Aluminum_Heat_Spreader_Paper_Template.pdf)
     
     Example: Heat spreader template
     
 32. Tape the heat spreader template down to the heat spreader and use the template to place your center punch to mark each hole.
 
 33. Drill each hole with a 5mm drill bit.
 
 34. Place the aluminum heat spreader into the mdf insulator board and use the heat spreader as a drill guide to drill the insulator board.
 
 35. Align the holes in the insulator board and heat spreader with the 519.5mm 20x20mm extrusions of the Z-Gantry.  Center the insulator board between the 2 gantry plates and clamp them together.
 
 36. Using the insulator and heat spreader as a drill guide, drill the 5mm holes in the 4 corners of the heat spreader.
 
 37. Remove the clamps and lay the heat spreader on a flat surface.
 
 38. Using a countersinking bit or a larger drill bit that is wider than the head of the M5 flat head screws drill countersinks for all 6 holes of the heat spreader. Make sure that the countersink is deep enough to keep the head of the flat head M5 screws below the surface of the aluminum heat spreader or you risk cracking the corner of the glass that clips on top.
 
     Example: Counter sunk hole
              All holes done
 
 39. Using a larger bit than the original 5mm, I'd say 6 or 7mm, drill out the 4 holes in the 519.5mm 20x20 extrusions to allow the heated bed adjustment to move without binding.
 
 40. Set the gantry assembly aside for now.
 
 41. Locate 4 M5x70mm flat head hex screws, 2 M5x30mm flat head hex screws, 6 M5 nylon lock nuts and 6 M5 oversized washers (15mm OD)
 
     Example: Hardware
 
 42. Lay the MDF insulator board flat with the top of the board facing up.  
 
 43. Position the 380mm square silicone heater in the center of the insulator board with the adhesive side up.
 
 44. Remove the adhesive backing.
 
 45. Thoroughly clean the back side of the aluminum heat spreader to ensure proper adhesion.
 
 46. Place the aluminum heat spreader on top of the heater pad taking great care to align the holes of the heat spreader with the holes in the insulator board.
 
 47. Press down firmly all over the heat spreader to ensure you have adhesion of the silicone heater to the aluminum heat spreader.
 
 48. Select one corner of the aluminum heat spreader and insert 1 M5x70mm flat head screw through the 5mm hole.
     
     Example: Screw inserted
     
 49. On the back side of the MDF insulator board slide 1 M5 oversized washer over the end of the screw and seat it against the MDF insulator board.
 
     Example: Washer installed
 
 50. Thread one M5 nylon lock nut on the end of the screw and tighten down.
 
     Example: Lock nut started
              Lock nut tightened
 
 51. Repeat steps 48 - 50 for each of the other 3 corners of the aluminum heat spreader.
 
 52. Select one of the middle holes in the heat spreader.
 
 53. Insert 1 M5x30mm flat head screw through the hole.
 
     Example: Screw inserted
 
 54. On the back side of the MDF insulator board slide 1 M5 oversized washer over the end of the screw and seat it against the MDF insulator board.
 
     Example: Washer installed
 
 55. Thread one M5 nylon lock nut on the end of the screw and tighten down.
 
     Example: Lock nut started
              Lock nut tightened
 
 56. Repeat steps 52 - 53 for the other middle hole of the aluminum heat spreader.
 
 57. Set this assembly aside for later use.
 
 58. Locate the printed parts "Z Leadscrew Bearing Holder Base" and "Z Leadscrew Bearing Holder Top", there should be 2 of each.
 
 59. Insert 1 608ZZ 8x22x7 bearing in each piece.
 
     **TIPS**
     
      * If the bearing won't fit because the hole it too tight then use a q-tip and acetone to wet the inside walls of the seating surface.  Repeat this until the walls are soft enough to allow you to press fit the bearings.
      * If the bearing fits but is loose then use thin kapton tape wrapped around the bearing evenly to shim the bearing into the holder.
    
    Example: Z axis top and bottom printed parts
 
 59. Locate:
      * Z-Gantry assembly
      * 2 36 tooth GT2 pulleys
      * 4 8mm shim washers
      * 2 12mm leadscrews
      * 2 delrin leadscrew nuts
      * 12 M5 standard washers
      * 4 M5x25mm socket cap screws
      * 8 M5x16mm button head screws
      * 4 M5 nylon lock nuts
      * 1 1164mm loop GT2 Belt
     
     Example: M5x16mm screws and washers
              36 tooth pulleys
              8mm washers
              1164mm closed loop belt
     
 60.  Starting at one side of the inside cross piece loosen one of the M5x10mm screws from the outer slots on the top of the cross piece. Set the screws aside as they aren't used here and were just being used to hold the T-Slot nuts in place.
 
 61. Place a Z Axis bottom bearing holder about 1 to 2mm from the corner of the cross piece and the V-Slot extrusion.
 
     Example: bearing piece placed correctly
  
 62. Place 1 M5 standard washer on 1 M5x16mm button head screw.
 
 63. Using a hex wrench or similar tool, slide a T-Slot nut under the bearing holder and line up the threads with the hole in the bearing holder.
 
 64. Insert the M5x16mm screw into the hole and tighten.
 
     Example: corner bearing holder mounteed
 
 65. Repeat steps 62 for the other hole in the bearing holder.
 
 66. Repeat steps 60 - 65 for the other side of the cross piece.
 
     Example: bottom bearing holders mounted
 
 67. Place 1 M5 standard washer on 1 M5x16mm button head screw.
 
 68. Insert a delrin leadscrew nut through the large hole on one side of the Z-Gantry assembly with the cylinder portion of the of the leadscrew nut passed through the bottom of the large hole in the gantry plate.
 
     Example: Leadscrew nut in place
 
 69. Insert the M5x16mm screw with washer through one of the top holes to secure the delrin leadscrew nut.
 
 70. Place a washer on the other side of the gantry plate on the screw passed through and use 1 M5 nylon lock nut to secure the screw but do not tighten just yet.
 
 71. Repeat steps 67 - 70 for the other screw hole of the leadscrew nut.
 
 72. Repeat steps 67 - 71 for the other side of the gantry assembly.
 
 73. Thread one 12mm leadscrew through one of the delrin leadscrew nuts with the longer tapered side facing the bottom of the Z-Gantry plate.  Thread this about halfway.
 
 74. Repeat step 73 for the other side of the gantry assembly.
 
 75. Slide one 36 tooth GT2 pulley on the longer tapered side of one of the lead screws with the collar facing the Z-Gantry assembly and tighten snugly.
 
 76. Repeat step 75 for the other leadscrew.
 
 77. Place 1 8mm shim washer on each of the bearings secured to the lower bearing holders mounted on the center cross piece of the main chassis.
 
 78. Holding the Z-Gantry assembly with the leadscrews inserted and the pulleys facing down slide the assembly onto the V-Slot aligning the wheels.  Feed the leadscrew through the 1164mm GT2 closed loop belt and then feed the remaining tapered end of each leadscrew through the 8mm shim washer and into the bearing underneath.
 
 79. Place 1 M5 standard washer on 1 M5x25mm socket head screw, repeat this for one more M5x25mm screw.
 
 80. Feed these screws through each of the holes of one of the Z axis top bearing holders.
 
 81. Secure 1 T-Slot nut on the end of each of the M5x25mm screws.
 
 82. Place 1 8mm shim washer on the top of the lead screw feeding the short tapered end of the lead screw through the hole of the washer.
 
 83. Feed the remaining portion of the taper through the bearing hole of the Z-Axis top assembly with the flat side of the bearing holder facing the V-Slot. As you are doing this you will need to take special care to feed the T-Slot nuts threaded on the M5x25mm screws into the left and right most slots of the V-Slot extrusion.
 
 84. Tighten the 2 M5x25mm socket head screws to firmly affix the top bearing holder to the V-Slot.
 
 85. Repeat steps 79 - 84 for the other side of the Z-Gantry/leadscrew.
 
     Example: Z Gantry installed
              Z Gantry installed
 
 86. Tighten the screws on each side of the leadscrew nuts.
 
     Tightening the leadscrew nuts
 
 87.  Align the belt with the 2 36 tooth pulleys.
 
 88. Use a bubble level to ensure that the Z Gantry is level.  This is essential before testing the z axis for binding. If the Z gantry is off level manually spin one of the lead screws to bring it into level.  If the leadscrew won't turn you have binding.  See the next step for tips.
 
 89. Level the Z axis. The Z axis must be level in all directions in order to spin freely.  The following are tips for leveling your Z axis.
    
      * If you have binding on either leadscrew, loosen the 2 screws holding the leadscrew nut to the Z gantry plate.
      * You can use a magnetic bubble level attached to the leadscrews to square them up.
      * The if you have lateral binding of the leadscrews to the left and right side you can loosen the bearing blocks at the bottoms and move them closer or further away from the V-Slot.
      * In some cases (when the Z Gantry holes for the delrin nut aren't true) you will need to sand material off of the seating surface of either the top or bottom bearing holders.
 
 90. Locate 1 printed motor mount, 1 nema 17 stepper motor, 4 M3x8mm button head screws and 4 M3 standard size washers.
     
     Example: Motor mount
              Nema 17 stepper motor
              Screws and washers
 
 91. Place the motor mount on top of the nema 17 motor as shown below.  Make sure that you pay close attention to the orientation of the wiring harness or plug on one side of the stepper motor.
 
     Example: Motor mount placed properly
    
 92. Place 1 M3 standard washer on 1 M3x8mm button head screw.
    
     Example: Screw and washer
 
 93. Insert the screw from step 91 into one of the holes of the motor mount and secure it to the stepper motor underneath.
 
     Example: Attaching the motor mount
 
 94. Repeat steps 92 - 93 for the remaining 3 holes of the motor mount.
 
     Example: Motor mount attached
 
 95. Locate these screws and T-slot nuts you inserted into the front slots of the center support.
 
     Example: 2 screws in the side and 2 in the top front slot
 
 96. Remove the M5x10mm button head screws that were used to hold the T-Slot nuts in place.
 
     Example: Temporary screws removed
 
 97. Place the motor mount on the center support as shown in the picture below.
 
     Example: Motor mount oriented correctly
 
 98. Using a hex wrench slide a T-Slot nut under one of the top holes in the motor mount.
 
     Example: T-Slot nut placed
     
 99. Locate 1 M5 standard washer and reuse one of the M5x10mm button head screws previously removed from the T-Slot nuts.  Install the washer on the screw.
 
     Example: Washer and screw
     
 100. Thread the screw through the motor mount and into the T-Slot nut underneath.  Tighten the screw.
 
 101. Repeat steps 98 - 100 for the other top hole of the motor mount.
 
      Example: Motor mount secured
 
 102. Using a hex wrench, slide a T-slot nut behind one of the holes on the motor mount that sits flush with the front of the center support.
 
 103. Locate 1 M5 standard washer and 1 M5x16mm button head screw. Install the washer on the screw.
 
 104. Thread the screw through the hole that you positioned the T-Slot behind and tighten it.
 
 105. Repeat steps 102 - 104 for the other hole in the motor mount.
 
      Example: Motor mount secured
      
 106. Locate the 2 printed parts Z Idler slide support, 4 M5 standard washers, 2 idler pulley kits, 1 20 tooth GT2 pulley, 2 M5x10mm button head screws and 2 M5x25mm socket cap screws
 
      Example: Z Idler slide support
               Idler pulley kits
               20 tooth GT2 pulley
               Screws
               
 107. Assemble the idler pulleys by press fitting one bearing into one side of the pulley.  Flip the pulley over and insert the nylon space in the center, aligning it with the hole in the bearing below it.  Then press fit the other bearing into the open side of the pulley.
 
      Example: Idler pulley
      
 108. Remove the M5x10mm button head screws in the remaining 4 T-Slot nuts installed in the center support and slide the T-Slot nuts out of the way, 2 to each side of center.
 
      Example: Remove these screws
      
 109. Choose one side of the center support and split 2 of the 2 slot nuts and place the Z idler slide support in between them.
 
      Example: Z idler slide support placed
      
 110. Using a hex wrench, slide the t-slot nut closest to the recessed screw hole under the hole so that the threads align with the screw hole in the printed part.
 
 111. Insert 1 M5x10mm screw in this hole and tighten.
 
      Example: Screw secured
      
 112. Using a hex wrench, slide the other T-Slot nut under the other hole in the Z idler slide support.
 
      Example: T-Slot nut placed
      
 113. Install 1 M5 standard washer on 1 M5x25mm socket cap screw.
 
      Example: Washer installed
      
 114. Insert the screw through the center hole of the idler pulley.
 
      Example: idler pulley installed
      
 115. Install 1 M5 standard washer on the screw, on top of the idler pulley.
 
      Example: Washer installed
      
 116. Thread the assembly through the non-recessed screw hole of the Z idler slide support and snug.
 
      Example: Install idler
      
 117. The idler pulley should be able to spin freely.
 
      Example: Z idler slide support installed
      
 118. Repeat steps 109 - 117 for the other side of the center support.
 
      Example: Z idler slide supports finished
      
 119. Install the 20 tooth GT2 pulley on the center motor shaft but do not tighten yet.
 
 120. Feed the flat side of the belt around the idler pulley as pictured.  Then wrap the tooth side around the GT2 pulley on the motor. Finally feed the flat side around the other idler pulley.  You will likely need to loosen the Z idler slide support to make this work but be sure to find the ideal tension and tighten them down again.
 
      Example: First idler pulley
               GT2 pulley
               Second idler pulley
               Adjusting tension
               
 121. Work the belt back and forth to help work the GT2 pulley onto the shaft of the stepper motor at the ideal height and then secure the GT2 pulley using it's set screws.
 
      Example: Pulley adjusted
 
 122. Ensure the belt is flat against the pulley and not catching on the edges as this can damage the belt.
 
 123. Install the solid state relay on the bottom rear inside extrusion using 2 of the T-Slot nuts you inserted previously.  Use 2 M5x12mm socket cap screws to secure this in place.  Depending on your SSR you may need to tap the holes to allow the M5 screws to feed through.
 
      Example: SSR and screws
               SSR installed
      
      * When you install the top side extrusions take care to align the 4 T-Slot nuts that are threaded on the M5x8mm button head screws with the 4 holes drilled in each extrusion and the slots in the V-slot verticals.  
      * Before tightening these screws make sure you measure 215mm from the front facing end of the extrusion to the edge of the V-Slot verticals to ensure proper alignment of the Z axis.
 
 124. Using the extrusion slot cover material, a sharp knife and a measuring instrument line all the slot channels that will be holding your plexiglass/acrylic covers if you are using them here.  Install the top extrusions into their respective sides to hole the plexiglass in.  If not using covers still install the top extrusions.
 
      Example: Channel covers
               Plexiglass installed
            
 125. Thats it for the Z axis and bottom chassis!

## X/Y Axis

 1. Locate 2 Corner Bearing Bracket A and 2 Corner Bearing bracket B printed parts.
 
    Example: Corner Bearing Bracket A
             Corner Bearing Bracket B
             
 2. Press fit 1 10mm (ID) x 22mm (OD) bearing into each of the bearing holes of the 4 printed corner bearing brackets.
    
    Example: Corner bearing brackets with bearings inserted
    
    * If the bearing holes are too tight, use acetone and a q-tip to wet the bearing hole walls until the abs is soft. Then press fit the bearing in.
    * If the bearing holes are too loose, wrap the outside wall of the bearing with a thin layer of kapton tape to shim the bearing.
    
 3. Starting with the front left top corner of the inside of the chassis place the corner bearing bracket that matches up with the holes drilled through the top extrusions.  This should be corner bearing bracket B.
    
    Example: Top left corner bearing bracket placed
    
 4. On each side of the bracket you should remove enough of the prepopulated M5x10mm button head screws from the t-slot nuts that were installed earlier to be able to secure each of the screw holes of the corner bearing bracket plate.
 
 5. Using a hex wrench slide 1 t-slot nut behind one of the inner most screw holes of the corner bearing bracket and secure it with 1 M5x10mm screw.  Make sure that the corner bearing bracket is flush with the corner of the extrusions.  This is necessary for proper X/Y alignment.
    
    Example: Inner most screw hole secured
    
 6. Repeat this process for all of the holes of the corner bearing bracket.
 
    Example: Bearing bracket secured
 
 7. Moving counter clockwise, repeat this process for the remaining 3 corners, take care to alternate corner bearing bracket versions each time.  e.g. Front right corner uses corner bearing bracket A.  Make sure the drilled holes in the extrusions line up with the corner bearing bracket's bearing holes.
 
    Example: Corner bearing brackets installed
 
 8. Locate 2 610mm x 10mm hardened precsion rods, 2 printed rod end knobs, 2 M3 standard nuts and 2 M3x8mm button head screws.
 
 9. Carefully insert 1 M3 nut into the hexagonal shaped recess on the inside of 1 printed rod end knob.
 
    Example: nut installed
 
 10. Slide the rod end knob onto one end of 1 610mm precision rod.
 
     Example: Rod end knob on precision rod
 
 11. Thread 1 M3x8mm button head screw through the screw hole of the rod end knob and tighten down enough to securely hold the rod end knob on the precision rod.
    
     Example: Rod end knob installed
    
 12. Repeat steps 9 - 11 for the other precision rod.
 
 13. Locate 1 XY Axis Belt Tensioner A, 1 XY Axis Belt Tensioner Block A, 2 M3x50mm socket head screw, 4 M3 nylon lock nuts, 1 M5 standard hex nut, 1 M5x16mm button head screw, 2 sintered bronze bushings and 2 M3x25mm socket cap screws.
 
 14. Press fit the bronze bushings into the large holes of the XY Axis Belt Tensioner printed part.
 
      * If the fit is too tight, use acetone and a q-tip to soften the inner wall of the printed part's bushing hole and then press the bushing in.
      * If the fit is too loose, use kapton tape to shim the bushing and then press the bushing in.
      
      Example: Bushing press fit into belt tensioner
      
 15. Thread 1 M3x50mm socket cap screw through one of the 3mm holes in the bottom of the XY Axis Belt Tensioner.
     
     Example: M3x50mm socket cap screw
              Completed XY Tensioner
              
 16. Repeat the process for the other hole.
  
 17. Fit the XY Belt Tensioner Block's 2 holes on the end of the 2 M3x50mm screws taking care to align the slot for the GT2 belt.
     
     Example: Belt Slot aligned
              Belt slot aligned
     
 18. Screw the screws through the tensioner block but not all the way.
  
 19. Screw on 1 nylon locknut on the end of each of the M3x50mm screws.
  
 20. Thread 1 M3x25mm through one of the belt slots.
  
 21. Screw on one nylon lock nut on the end of the screw but do not tighten.
  
 22. Repeat steps 10 - 11 for the other belt retension screw hole.
  
 23. Insert the M5 standard hex nut into the slot on top of the XY Axis Belt Tensioner.
     
     Example: Completed XY Tensioner
     
 24. Thread 1 M5x16mm button head screw through the recessed screw hole and thread the screw into the nut in the opposing side of the tensioner. DO NOT TIGHTEN! You will crack the part!!!  Just let the threads grab.
  
 25. The finished assembly will look like this:
 
     Example: Completed XY Tensioner
  
 26. Repeat these steps for the other XY Axis Belt Tensioner A piece as well as the other 2 XY Axis belt tensioner pieces.  
  
 27. Set them aside for now.
  
 28. Locate the dual hotend carriage printed part.
 
     Example: Hot end carriage
  
 29. Insert M3 standard nuts into each of the slots of the carriage making sure to press them in until they are fully seated.
  
 30. Using the q-tip or kapton tape method described in step 14 press fit 1 10mm sintered bronze bushing into each busching hole of the carriage taking care to ensure that they're fully seated level or you will have binding issues.  Test the alignment by inserting a 512mm precision hardened rod into one of the axis and move the carriage up and down the shaft.  It should move as if there were a cushion of air between the bushing and the rod.
  
     * If you have minor binding you can insert one of the 512mm hardened precision rods into an electric drill and insert the precision rod into one of the carriage axis.  Then start spinning the rod slowly with the drill while moving the carriage up and down the shaft to force the self aligning bushings into alignment.
     * If you have major binding you can set the rod end on a hard surface and gently knock the bushing in by knocking the carriage into the hard surface.  Take care not to knock too hard or you could crack the carriage.
  
 31. Insert 1 512mm precision hardened rod through each axis of the carriage and set on a flat surface with the flat side of the carriage facing up and the end of the carriage that will house the hotends facing you.  This is the orientation of the carriage in the chassis when you are looking at the front.
     
     Example: Carriage placed flat
              Carriage oriented correctly
 
 32. Slide the large precsion rod hole of 1 XY belt tensioner A onto the right end of the rod assembly with the bushings on the top side of the tensioner.
    
     Example: Tensioner A placed correctly
              Tensioner A placed correctly
    
 33. Slide the large precision rod hole of 1 XY belt tensioner B onto the left end of the rod assembly with the bushings on the top side of the tensioner.
     
     Example: Tensioner B placed correctly
     
 34. Slide the large precision rod hole of 1 XY belt tensioner A onto the front end of the rod assembly with the bushings on the bottom side of the tensioner.
    
     Example: Tensioner A placed correctly
    
 34. Slide the large precision rod hole of 1 XY belt tensioner B onto the back end of the rod assembly with the bushings on the bottom side of the tensioner.
  
     Example: Tensioner B placed correctly
  
 35. Gently tighten the M5x16mm screw.  Take care not to over tighten because you will crack the part.  It only needs to be snug.
  
     * If you over tighten any of the screws and the part cracks you can remove the part and slightly bend it to expose the crack and then apply a small drop of acetone into the crack then use a clamp to hold the piece together until the acetone sets and the acetone glue is hardened.
      
 36. This will be the orientation you will install the XY axis in the chassis.
  
     Example: XY assembly oriented correctly
  
 37. Locate 2 10mm shim washers, 1 610mm precision hardened rod and 2 32 tooth GT2 pulleys
  
 38. Starting with the front left rod, using the precision hardened rod you installed a rod end knob on, slide the rod into the hole drilled through the front extrusion.
     
     Example: Assembling the XY left side to the chassis
     
 39. As the rod enters the inside of the chassis install 1 10mm shim washer and then 1 32 tooth pulley with the teeth closest to the inside face of the extrusion.
     
     Example: Pulley
     
 40. Keeping the orientation that was previously established for the carriage feed the rod through the sintered bronze bushings of the XY tensioner B taking care to ensure that the bushings are on the top side of the tensioner.
     
     Example: Assembling the XY left side to the chassis
     
 41. Before feeding the other end of the rod into the bearing in the opposite side corner bearing bracket insert a 32 tooth pulley with the tooth side facing the corner bearing bracket.
  
     Example: Pulley
  
 42. Install a 10mm shim washer, then slide the end of the rod into the bearing.
  
 43. Repeat steps 27 - 32 for all 4 rods making sure to keep things as aligned as possible.  The rods with the rod end knobs should be used for the 2 rods that go on the front left side and the left front side extrusions.
  
 44. Locate one 1 meter section of GT2 belt.
  
 45. Choose one side of the chassis and slide the end of the belt into the slot of the XY belt tensioner block taking care to slide the belt into the block until it is fully seated and the teeth of the belt have engaged in the block's teeth thus keeping the belt locked in place.
  
 46. Locate 1 M3x25mm socket cap screw and 1 nylon lock nut.
  
 47. Thread the screw through the screw hole in the tensioner block and install the nylon lock nut on the screw end.
  
 48. Tighten the lock nut until the screw is snug, do not over tighten or you will crack the printed part.
  
 49. Pass the GT2 belt around the 32 tooth pulley on the side of the block that you installed the belt end into.
  
 50. Stretch the belt over the opposing 32 tooth pulley and back around to the XY belt tensioner.
  
 51. Cut the belt to length leaving enough belt to fit through the belt slot of the tensioner to help with seating the belt.
  
 52. Slide the belt end into the belt tensioner slot and seat the belt completely making sure that the teeth of the belt seat inside of the belt tensioner.
  
 53. Locate 1 M3x25mm socket cap screw and 1 nylon lock nut.
  
 54. Thread the screw through the screw hole in the tensioner and install the nylon lock nut ont he screw end.
  
 55. Tighten the lock nut until the screw is snug.  Do not over tighten or you will crack the printed part.
  
 56. Now using a hex wrench and 5.5mm socket wrench adjust each of the 50mm socket cap screws that run through the tensioner and tensioner block until the belt is tight but not guitar string tight.
     
     Example: Belt complete
     
 57. Repeat steps 35 through 46 for the remaining 3 sides.
  
 58. You should now be able to use the 2 rod end knobs on the front and left side to move the XY carriage, like an Etch-a-sketch.

## Front door assembly

 1. Locate 2 407.5mm 20x20mm extrusions
 
 2. Carefully tap each end of the extrusions
    
    Example: Tapped extrusion end
    
 3. Thread 1 M5x10mm button head screw into each end of each of the extrusions leaving approximately 3mm of thread showing.
 
 4. Locate the 20x20mm drill guide.
 
 5. Locate 2 567.5mm 20x20mm extrusions.
 
 6. Carefully tap each end of the extrusions.
 
 7. Using 3 M5x8mm button head screws and 2 T-Slot nuts install the drill guide on one of the 567.5mm extrusions.
    
    Example: Drill guide 1
             Drill guide 2
    
 8. Drill the first hole on one side of the extrusion drill guide through the extrusion.
    
    Example: Drill this hole
             Hole drilled
    
 9. Repeat steps 7 - 8 for each end of the 2 567.5mm 20x20mm extrusions.
 
 10. On a flat surface place one 567.5mm 20x20mm extrusion laying horizontal with the holes that were drilled facing toward you and away from you.
 
 11. Locate the 2 407.5mm 20x20mm extrusions that were previously tapped.
 
 12. on each end of the 567.5mm extrusion insert the head of the socket cap screw of each of the 407.5mm extrusions making a "U" shape.
 
     Example: Extrusions placed
 
 13. Keeping the extrusions flush on the edge pass a hex wrench through the drilled holes and tighten the button head screws.
     
     Example: Tightened down
     
 14. Lay the tightened door assembly down on a flat surface with the opening of the "U" facing away from you.
    
     Example: Orientation
    
 15. On the top side of the left 407.5mm extrusion insert 4 T-Slot nuts and hand tighten 1 M5x8mm flat head hex screw into each one to keep them from sliding.
 
     Example: T-Slot nuts placed
 
 16. On the top side of the right 407.5mm extrusion insert 2 T-Slot nuts and hand tighten 1 M5x16mm button head screw into each one to keep them from sliding.
 
     Example: T-Slot nuts placed
 
 17. Locate a section of T-Slot cover, a sharp knife and a measuring instrument.
 
 18. Measure and install the T-Slot cover upside down in each of the inner channels to hold the clear plexiglass cover.
 
     Example: T-Slot covers installed
 
 19. Install the plexiglass cover in the channels of the U.
 
 20. Slide the remaining 567.5mm 20x20mm extrusion onto the ends of the button head screws of the open side of the U shape and keep the edges flush while tightening down the assembly.
     
     Example: Cover installed
     
 21. Locate 2 extrusion hinges.
 
 22. Face the main chassis assembly, looking at the front side.
 
 23. On the left front corner 20x20mm vertical extrusion on the main chassis install 4 T-Slot nuts and hand tighten 1 M5x8mm flat head screw into each to keep them from sliding.
     
     Example: Preinstall screws
     
 24. Install the 2 extrusion hinges on the main chassis using the 4 T-Slot nuts and 4 5x8mm flat head screws installed in the previous step.
 
     Example: Installed hinges
 
 25. Using the 4 T-Slot nuts and 4 M5x8mm flat top screws previously installed on the front door, install the door on the main chassis.
     
     Example: Hinges attached to the door
              Door installed
     
 26. Locate the plastic door handle or a printed handle.
 
 27. Using the 2 T-Slot nuts and 2 M5x16mm button head screws installed previously in the right side of the front door, install the handle.
 
     Example: Handle Installed

## Top cover assembly

 1. Locate 4 330mm 20x20mm extrusions, 7 569.5mm 20x20mm extrusions, 1 100mm 20x20mm extrusion, 1 55mm 20x20mm extrusion and 1 515mm 20x20mm extrusion.
 
 2. Carefully tap each end of all of the extrusions with an M5 x .8mm tap.
 
 3. Thread an M5x10mm button head screw into the end of each of the 7 569.5mm 20x20mm extrusions and 1 515mm 20x20mm extrusion leaving only 2mm of thread showing.
 
 4. Thread an M5x10mm button head screw into one end of the 100mm 20x20mm extrusion and 55mm 20x20mm extrusion leaving only 2mm of thread showing.
 
 5. Locate the 20x20mm extrusion drill guide.
 
 6. Using 3 M5x8mm button head screws and 2 T-slot nuts install the drill guide on the end of 1 330mm 20x20mm extrusion.
 
 7. Carefully drill the first hole near the end of the extrusion on both sides of the extrusion using a 5mm drill bit.
 
 8. Repeat this process for each end of the 4 330mm 20x20mm extrusions.
 
 9. Install the drill guide on the end of the 100mm 20x20mm extrusion that doesn't have the M5x10mm screw threaded into it.
 
 10. Carefully drill the first hole near the end of the extrusion on only one side.
 
 11. Repeat steps 9 - 10 for the end of the 55mm 20x20mm extrusion.
 
 12. Locate 1 330mm 20x20mm extrusion and measure 110mm from one end, on once side, and mark with a center punch or other device to leave a clear mark that will help with drilling.
 
 13. Carefully drill straight through the extrusion. This is only done on one extrusion and makes this extrusion the front right corner of the lid.
 
 14. Locate 1 515mm 20x20mm extrusion, 1 100mm extrusion and 1 55mm extrusion.
 
 15. Place the 515mm 20x20mm extrusion on a flat surface.
 
 16. Slide the button head screw on the left side of the 515mm extrusion into the slot of the 100mm extrusion with the hole drilled through until the extrusions are flush.
 
 17. Pass a hex wrench through the hole of the 100mm extrusion and tighten the M5x10mm screw down making sure to keep things flush and flat.
 
 18. Locate the 55mm extrusion.
 
 19. Slide the end of the 55mm extrusion with the hole drilled through it over the M5x10mm button head screw at the end of the 100mm extrusion lining up the hole in the 55mm extrusion with the button head screw.
 
 20. Pass a hex wrench through the hole of the 55mm extrusion and tighten the button head screw down while keeping things flush and flat.
 
 21. Locate the 330mm extrusion that was drilled not only near the ends but also drilled 110mm from one end through the slot.
 
 22. Slide the 330mm extrusion over the M5x10mm button head screw util the end of the extrusion is lined up with the bottom of the 515mm extrusion and the hole drilled through the 330mm extrusion is lined up with the button head screw of the 55mm extrusion.
 
 23. Pass a hex wrench through the middle hole and tighten the M5 screw keeping things flush and flat.
 
 24. Locate 3 569.5mm extrusions and place them in the shape of a U with the opening of the U facing the right.
 
 25. If you want to install a lift handle on the front face of the lid, on the front face of the 20x20mm extrusion insert 2 T-Slot nuts and tighten 1 M5x16mm button head screw into each to keep them from sliding.
 
 26. If you are installing the sliding hinge on the lid, on the front face of the 20x20mm extrusion insert 1 T-Slot nut and thread 1 M5x16mm button head screw into it and tighten enough to keep things from sliding.
 
 27. Insert 2 T-Slot nuts and hand tighten 1 M8x8mm flat top screw in the left facing slot of the left extrusion.  This is for the hinges.
 
 27. Place the assembly with the 55, 100 and 515mm extrusions tightend to it on the opening of the U and slide the button head screw of the front right end through the 330mm extrusion.
 
 28. Pass a hex wrench through the bottom hole of the 330mm extrusion and tighten, take care to make sure things are flush and flat.
 
 29. Locate 3 330mm 20x20mm extrusions.
 
 30. Slide one end of a 330mm extrusion over the button head screws at each of the 3 other corners of the lid assembly.
 
 31. Using a hex wrench passed through the holes drilled through these extrusions tighten all of the screws down keeping things flush and flat.
 
 32. Locate some T-Slot covers, a sharp knife and measuring device.
 
 33. Carefully measure and insert the T-Slot covers into the inner channels of the whole assembly to pad the channels for housing the covers.
 
 34. Install the 4 clear side panels in the lid.
 
 35. Install T-Slot covers in the 4 remaining 569.5mm extrusions on 2 of the faces next to each other.
 
 36. Install 3 of the 569.5mm extrusions on the lid top on the rear, left and right sides.
 
 37. Passing a hex wrench through the drilled holes in the vertcial 330mm extrusions tighten the 3 installed extrusions.
 
 38. Loosen the bottom front screws to allow the front two verticals to move outward.  This is just to install the top clear panel.
 
 39. Slide the top clear panel and ensure it is fully seated in the rear, left and right channels.
 
 40. Install the remaining 569.5mm extrusion on the top front of the cover and tighten all M5 screws in all of the top and bottom corners.
 
 41. Locate 2 aluminum extrusion hinges.
 
 42. Using the preinstalled T-Slot Nuts and M5x8mm flat top screws install the hinges in the front and rear corners of the left side of the lid and chassis.
 
 43. Locate a plastic handle or a printed handle.
 
 44. Using the preinstalled T-Slot nuts and M5x16mm button head screws install the handle on the lid.
 
 45. Locate the printed sliding hinge.
 
 46. Using the preinstalled T-Slot nuts and M5x16mm buttn head screws install the hinge but before tightening down the sliding piece of the hinge open the lid until it is opened to the point that you like, then tighten down the last screw.
 
 Thats it! the Mechanincal

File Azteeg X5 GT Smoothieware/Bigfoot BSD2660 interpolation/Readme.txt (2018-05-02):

The spreadsheet used to determine register values can be found at the following link: 
https://www.kreativ-fraesen.de/technisches/3d-drucker/stepper-driver-tmc2660-en/

Modifications to the original TMC2660 settings provided by Kreativ-fraesen on this 
spreadsheet were made by altering green values in the spreadsheet tabs and adding 
lines to the config file corresponding to the calculated register hexadecimal value using:

motor_driver_control.alpha.reg 00204,981C0,A0000,C000E,E0060
motor_driver_control.beta.reg 00204,981C0,A0000,C000E,E0060
motor_driver_control.gamma.reg 00204,981C0,A0000,C000E,E0060

The configuration shown above allows for step generation at 1/16 microstepping and
driver-performed interpolation to 1/256. The result is a (much) quieter running
system where microstepping isn't limited by processor step generation. My initial tests
have shown equal performance for driver-enabled interpolation, no interpolation, and 
1/64 on-board microstepping (4x steps/mm) when printed using identical g-code 

Note: The config is for a system with X and Y steps per mm of 100 and Z steps @ 720/mm
(at 1/16 microstepping) with drivers running at 1.0A.

The stock Herculien runs X, Y and Z @ 80, 80, and 2880 steps/mm @ 1/16 microstepping. Be
sure to alter the config file accordingly before use in your system.

Directly editing the driver registers without knowing what you are doing can lead to
nonsensical and potentially damaging results. Do this at your own risk.

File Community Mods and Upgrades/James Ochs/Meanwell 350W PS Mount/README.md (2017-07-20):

Meanwell 350W Power Supply Mount for Herculien
==============================================

The Meanwell 350W power supply has different dimensions than the 450W version.  The printed brackets on the bottom in the Herculien BOM work fine, but the 350W version is much narrower than the 450W, and therefore the upper bracket does not fit.  In addition, on the 450W version, the terminals face out from the side of the power supply, while the 350 watt version faces toward the back of it (I am considering the side with the fan and vents on it as the back due to the orientation of the power supply in the Herculien.)  This means that, if you are putting in acrylic/Lexan walls, the terminals would be inaccessable once the panel goes in.

This mod builds a small frame around the power supply and creates a small sliding window that can be opened to allow access to the terminals, but also protects them from anything accidentally falling into the back of the printer.  The 350W power supply will be installed in the same orientation as the 450W, with the fan facing the back of the printer frame.  The terminals should be on the left side, away from the right side wall if you are facing the frame from the front.  All right/left/top/bottom directions are based on the viewer standing at the front of the printer, looking toward the back, unless otherwise noted.

The instructions below assume that you have not yet completed the top section of the printer frame.  If you are reading this prior to completing the bottom section of your frame, you can add two T-slot nuts to the top of the Back Rear 20 x 80 extrusion before assembling the bottom frame, and you won't need the drop in ones.  If you've already put together the top section of the frame, you can use a 90 degree angle bracket to secure the 272mm extrusion to the right rear upright instead of drilling a hole and using a screw in the end.

Tools Required
==============

Hex allen key for M5 Screws
Hex allen key for M4 Screws

Parts Required
==============

1 20 x 20 x 272mm extrusion (This can be longer if you want a bigger window.  You will need to adjust your acrylic/Lexan size accordingly)
1 20 x 20 x 136mm extrusion
1 20 x 20 x 116mm extrusion
3 90 degree angle brackets for 20 x 20 extrusions
4 M4 x 12mm screws
2 M5 x 10mm button head screws
6 M5 x 8MM button head screws
4 M5 T-Slot nuts
2 M5 Drop-in T-Slot nuts (I've found the Misumi ones are the nicest)
1 peice of acrylic/Lexan 87mm x 128mm (you should be able to cut this out of scrap left over from cutting the other panels)
a little less than 500mm HSCA5 slot covers
2 x Power Supply Bracket 2 from the original BOM (Printed)
2 x Power Supply Bracket from this mod (Printed)

Metal Preparation
=================

Using the 20x80 8 hole drill guide drill a hole in the right rear upright.  The hole should be centered at 205mm from the bottom end of the extrusion.  

Using an M5 tap, tap both ends of the 272mm extrusion, and one end of the 136mm extrusion.

Secure the 20 x 20 drill guide to one end of the 136mm extrusion using 3 M5 x 8mm screws and 2 M5 T-Slot nuts.  Drill a 5mm hole using the first hole from the end through the extrusion.  

If you want, cut out the center section of the top of the 136mm extrusion (from the end to the hole, see photo) to create a channel for the acrylic/Lexan to fit in.  I used a bandsaw for this, but a hacksaw or dremel probably would work too.  This will make the cuts in the acrylic/Lexan easier.

20x20 Slotted End

Assembly
========

Attach both of the Power Supply Bracket 2 to the bottom of the power supply with 2 M4 x 12 screws. Using the two M5 x 8mm and M5 T-slot nuts previously installed on the 20 x 80 extrusions at the bottom rear of the frame, secure the power supply to the frame with the right side of the power supply.

Insert an M5 x 10mm screw into both ends of the 272mm extrusion, leaving 2-3mm of threads exposed.
Insert 2 M5 T-Slot nuts into the front side of the 272mm extrusion

In the 116mm extrusion attach two 90 degree angle brackets using two M5 T-Slot nuts and two button head M5 x 8mm screws on the same face of the extrusion.  

Attach an M5 x 8mm screw and T-slot nut to one of the angle brackets on the 116mm extrusion. 

Slide the T-slot nut into the bottom of the 272mm extrusion so that the two angle brackets are on the side of the 116mm extrusion facing towards the left as you are looking at it.  Tighten down the angle bracket somewhere in the middle of the 272mm extrusion to keep it from sliding around.

On a flat surface, slide the 136mm extension over the screw in the end of the 272mm extrusion.  The 90 degree angle brackets on the 16mm extension should be facing away from the 136mm extrusion.

Using the hole drilled in the end of the 136mm extrusion and the allen key tighten the screw down ensuring the ends of the extrusion are flush on all sides.

Insert an M5 x 8mm button head screw into the remaining 90 degree angle bracket and secure it to the left side of the 136mm extrusion on the left.  Both this bracket, and the right facing one on the bottom of the other 116mm extrusion should be secured so that they are a few mm above the end of the extrusion.

Loosely attach the two drop-in M5 T-Slot nuts to the bottom of the 90 degree angle brackets on the bottom of the 46mm extrusions.

Secure the 2 Power Supply Brackets from this mod to the 2 T-slot nuts on the front side of the 272mm extrusion

You should now have something that looks like an F with the remaining power supply brackets attached to the front of it.

Back View: Assembly Rear View

Front View: Assembly Front View

Insert the slot covers into the left side of the center 116mm extrusion and the right side of the left mm extrusion, and place 128mm peices of slot cover in the bottom of the 272mm extrusion and the top of the 20 x 80 extrusion, approximately in front of the terminals of the power supply.

Insert the acrylic/Lexan into the F shaped assembly and move the center extrusion into place to hold it.

Slide the screw at the end of the 272mm extrusion down the left side of the right rear upright until it is in postion The 46mm extrusions should be touching the 20 x 80 rear bottom extrusion and the acrylic/Lexan should be seated into all four sides.  If you have already built the top section, then you can use a 90 degree angle bracket and a drop in nut to secure the "F" assembly to the right rear upright on the frame.

Slide the two 90 degree angle brackets down to the 20 x 80 extrusion and tighten the screws into place.

Loosen the top two power supply brackets and slide them into place.  Secure the power supply brackets to the power supply using 2 M4 x 12mm screws, and tighten the M5 x 8mm screws attaching it to the 272mm extrusion.

Finished Installation:

Completed Installation

Usage
======

When you need access to the power supply terminals, loosen the two screws attaching the center 116mm extrusion to the top and bottom extrusions.  You should be able to slide it out of the way, and slide the acrylic/Lexan with it, exposing the terminals. 

Closed: Closed Cover

Open: Open Cover

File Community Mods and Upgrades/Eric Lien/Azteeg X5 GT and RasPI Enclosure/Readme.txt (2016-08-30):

So I am playing with a fun new (unreleased) controller and some drivers from +Roy Cortes??? at Panucatt. Dual extruder capable smoothieware based unit. I have been waiting to try this thing for a while. Just my luck. I get everything installed and now I have to travel for work next week. Guess I need to get some energy drinks and do my initial testing and tuning before I go.

My Panucatt azteeg x3 has served me so well. It was sad to pull it off its home of so many years. But I am certain just like Roy's other boards this new board will be a bomb proof workhorse. And his new driver design/footprint is just amazing.

My old front mounted hinged controller box and Viki LCD was just a little bit too tight a fit for the new board. So I designed a new box for the side of HercuLien which mounts the board above a Raspberry Pi3 running Octoprint and a new viki2 mount for the front.

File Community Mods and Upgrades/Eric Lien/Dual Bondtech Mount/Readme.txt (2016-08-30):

I finally did something I have been meaning to do for a while. My old HercuStruder design allowed for mounting my second extruder onto the 20x20 upright extrusion since the face of the extruder sits flush with the extrusion. But the Bondtech housing does not allow for this since the clamp holds onto the planetary section of the stepper so the Bondtech housing sits forward of the face of the extrusion. I have my control box sitting out front on a hinge, it can swing out of the way to open the front door. This would swing it back into the second Bondtech. I have had it hacked to work for a while... but I finally got around to making a new mount. The model is odd looking but places both extruders exactly how I wanted them. It was as compact as I could get things while still allowing both QR hinges to swing independently. 

The only pain is that to make the print as strong as possible it should be printed laying down, so that requires a fair amount of support. This is no issue for Simplify3D. But with other slicers YMMV.

It is designed to use brass thermal set inserts in the back side to clamp it together. So depending on the size inserts you have the size of this pocket hole may need adjustment. Also please don't judge my modeling on this one. The solidworks design tree is atrocious, but I was in a hurry to finally get this done and so took a few shortcuts.

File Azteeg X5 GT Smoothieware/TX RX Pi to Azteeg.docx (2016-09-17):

From Roy:
Login using SSH

Type

sudo apt-get update

When it done type

sudo apt-get upgrade

When done edit the file /boot/config.txt by typing

sudo nano /boot/config.txt

Scroll to the end then add this line(this diables bluetooth only, guide above disables wifi as well)

dtoverlay=pi3-disable-bt

Save file CRTL X then Y then enter

Type

raspi-config

Go to Advanced settings then Serial then it'll ask if you want console on Serial - select NO. Exit raspi config then reboot.

Connection

RPi --> X5

TX --> RX

RX --> TX

GND --> GND

From Octoprint webpage go to settings then add this to serial ports

/dev/ttyAMA0

Save then refresh octoprint main page for new setting to show up. select it and 115200 baud rate then connect. Sometimes you may need to reset the X5 to initialize properly.

I tried the Zero but its slow and camera it hit and miss. Definitely go with RPi 3. I also found out that my RPi 3 power adapter is flaky and would get disconnects or comm errors specially when the camera is connected so I replaced it with a better one and works ok now. I will eventually use a cheap DC-dc step down inside the case to power the RPi so it can be connected to the main power supply.

From Me: I connected pins 6 8 10 on the pi.


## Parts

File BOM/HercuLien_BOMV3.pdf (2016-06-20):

ITEM NO. | Subassembly QTY. Per | Qty Total | PART NUMBER | DESCRIPTION | Supplier 1: Links & Price ea. | Supplier 2: Links & Price ea.
1 | 1 | | Herculien_Frame (Subassembly)
1.1 | 4 | 4 | HFS5-2020-609.5(holes_added) | 20mmx20mm609.5mm aluminum extrusion for vertical supports at the corners. Extrusions requires holes be drilled. 3d model for drill guide available. | $15.00 / 1500mm (http://goo.gl/Rn3xYc#) | $3.47 (http://goo.gl/J2SwBg#)
1.2 | 2 | 2 | HFS5-2080-569.5 (SidesBottom_Holes) | 20x80x569.5mm aluminum extrusions. | $30.00 / 1500mm (http://goo.gl/Rn3xYc#) | $11.90 (http://goo.gl/2LajE3#)
1.3 | 1 | 1 | HFS5-2080-569.5 (LeftTop_Holes) | 20x80x569.5mm aluminum extrusions. | $30.00 / 1500mm (http://goo.gl/Rn3xYc#) | $11.90 (http://goo.gl/2LajE3#)
1.4 | 1 | 1 | HFS5-2080-569.5 (RightTop_Holes) | 20x80x569.5mm aluminum extrusions. | $30.00 / 1500mm (http://goo.gl/Rn3xYc#) | $11.90 (http://goo.gl/2LajE3#)
1.5 | 3 | 3 | HFS5-2080-569.5 (Default_No Holes) | 20x80x569.5mm aluminum extrusions. | $30.00 / 1500mm (http://goo.gl/Rn3xYc#) | $11.90 (http://goo.gl/2LajE3#)
1.6 | 1 | 1 | HFS5-2080-569.5 (BackTop_Holes) | 20x80x569.5mm aluminum extrusions. | $30.00 / 1500mm (http://goo.gl/Rn3xYc#) | $11.90 (http://goo.gl/2LajE3#)
1.7 | 1 | 1 | HFS5-2080-569.5 (FrontTop_Holes) | 20x80x569.5mm aluminum extrusions. | $30.00 / 1500mm (http://goo.gl/Rn3xYc#) | $11.90 (http://goo.gl/2LajE3#)
1.8 | 2 | 2 | V-Slot_20mmX80mm489.5mm | 20mmx80mmx489.5mm Vslot Extrusion | $20.00 / 1000 (http://goo.gl/Rn3xYc#) | $20.00 / 1000 (http://goo.gl/Sfh98b#)
1.9 | 16 | 16 | HNTTSN5-5 | T-Slot Nuts | $0.20 (http://goo.gl/D3hXRs#) | $28.00 / 100 (http://goo.gl/rpT76t#)
1.1 | 6 | 6 | Optional: HSCA5-R_460mm | T-SLot Covers (To Hold Clear Panels) | $3.00 / 1000mm (http://goo.gl/pXWmzj#) | $2.38 / 2000mm (http://goo.gl/ah7sAE#)
1.11 | 6 | 6 | Optional: HSCA5-R_569.5mm | T-SLot Covers (To Hold Clear Panels) | $3.00 / 1000mm (http://goo.gl/pXWmzj#) | $2.38 / 2000mm (http://goo.gl/ah7sAE#)
1.12 | 1 | 1 | Optional: 4.3mm thick Acrylic_or_Polycarbonate_Rightside_Panel | http://goo.gl/oR3krK | $15.70 (24"x24") (http://goo.gl/vB65Mp#)
1.13 | 1 | 1 | Optional: 4.3mm thick Acrylic_or_Polycarbonate_Leftside_Panel | http://goo.gl/YAD9aY | $15.70 (24"x24") (http://goo.gl/vB65Mp#)
1.14 | 1 | 1 | Optional: 4.3mm thick Acrylic_or_Polycarbonate_Backside_Panel | http://goo.gl/BmHRNU | $15.70 (24"x24") (http://goo.gl/vB65Mp#)
1.15 | 72 | 72 | 91239A224 | 5mm x 10mm button head screw | $7.93 / 100 (http://goo.gl/gNzWFp)
1.16 | 16 | 16 | 94500A230 | 5mm x 8mm button head socket cap screw | $6.15 / 50 (http://goo.gl/exEVR6#)
2 1 | | | Top_Cover (Subassembly) (Optional, not needed for printer function)
2.1 | 3 | 3 | HFS5-2020-300 | 20x20x300mm Extruded Aluminum | $10.00 / 1000mm | $1.71 (http://goo.gl/0uMwHC#)
2.2 | 1 | 1 | HFS5-2020-300 (configuration) | 20x20x300mm Extruded Aluminum | $10.00 / 1000mm (http://goo.gl/Rn3xYc#) | $1.71 (http://goo.gl/uF3Bic#)
2.3 | 8 | 8 | HFS5-2020-569.5 | 20x20x569.5mm Extruded Aluminum | $15.00 / 1500mm (http://goo.gl/Rn3xYc#) | $3.24 (http://goo.gl/m5MVLF#)
2.4 | 1 | 1 | HFS5-2020-515 | 20x20x515mm Extruded Aluminum | $15.00 / 1500mm | $2.93 (http://goo.gl/fW82FB#)
2.5 | 1 | 1 | HFS5-2020-100 | 20x20x100mm Extruded Aluminum | from drop cut (http://goo.gl/Rn3xYc#) | $3.03 (http://goo.gl/w7fIvp#)
2.6 | 1 | 1 | HFS5-2020-54.5 | 20x20x54.5mm Extruded Aluminum | from drop cut (http://goo.gl/Rn3xYc#) | $3.03 (http://goo.gl/BpjSgE#)
2.7 | 4 | 4 | HHPSN5 | Hinge for 20x20 Extrusion | $5.60 (http://goo.gl/a2ZCKD#)
2.8 | 20 | 20 | HNTTSN5-5 | T-Slot Nuts | $0.20 (http://goo.gl/D3hXRs#) | $28.00 / 100 (http://goo.gl/rpT76t#)
2.9 | 5 | 5 | HSCA5-R_300mm | T-SLot Covers (To Hold Clear Panels) | $3.00 / 1000mm (http://goo.gl/pXWmzj#) | $2.38 / 2000mm (http://goo.gl/ah7sAE#)
2.10 | 1 | 1 | HSCA5-R_515mm | T-SLot Covers (To Hold Clear Panels) | $3.00 / 1000mm (http://goo.gl/pXWmzj#) | $2.38 / 2000mm (http://goo.gl/ah7sAE#)
2.11 | 1 | 1 | HSCA5-R_98mm | T-SLot Covers (To Hold Clear Panels) | $3.00 / 1000mm (http://goo.gl/pXWmzj#) | $2.38 / 2000mm (http://goo.gl/ah7sAE#)
2.12 | 1 | 1 | HSCA5-R_48.5 | T-SLot Covers (To Hold Clear Panels) | $3.00 / 1000mm (http://goo.gl/pXWmzj#) | $2.38 / 2000mm (http://goo.gl/ah7sAE#)
2.13 | 1 | 1 | HSCA5-R_200mm | T-SLot Covers (To Hold Clear Panels) | $3.00 / 1000mm (http://goo.gl/pXWmzj#) | $2.38 / 2000mm (http://goo.gl/ah7sAE#)
2.14 | 11 | 11 | HSCA5-R_569.5mm | T-SLot Covers (To Hold Clear Panels) | $3.00 / 1000mm (http://goo.gl/pXWmzj#) | $2.38 / 2000mm (http://goo.gl/ah7sAE#)
2.15 | 4 | 4 | HFC5-2020-B | Extrusion Endcap | $1.88 (http://goo.gl/VBXGv2#)
2.16 | 3 | 3 | .177in thick Acrylic or Polycarbonate Left Front Back Cover | http://goo.gl/mjZ4er (http://goo.gl/mjZ4er#) | $15.70 (24"x24") (http://goo.gl/vB65Mp#)
2.17 | 1 | 1 | .177in thick Acrylic or Polycarbonate Right Cover | http://goo.gl/rPAJGD (http://goo.gl/rPAJGD#) | $15.70 (24"x24") (http://goo.gl/vB65Mp#)
2.18 | 1 | 1 | .177in thick Acrylic or Polycarbonate Split Top Cover | http://goo.gl/l9hLrq (http://goo.gl/l9hLrq#) | $15.70 (24"x24") (http://goo.gl/vB65Mp#)
2.19 | 24 | 24 | 91239A224 | 5mm x 10mm button head socket cap screw | $7.93 / 100 (http://goo.gl/gNzWFp#)
2.20 | 16 | 16 | 91294A207 | 5mm x 8mm flat head socket cap screw | $6.75 / 100 (http://goo.gl/qvo2ic#)
2.21 | 2 | 2 | 1078A311 | Plastic Handle | $3.76 (http://goo.gl/qdXnO0#)
2.22 | 2 | 2 | 90965A160 | 5mm stainless flat washer | $4.62 / 100 (http://goo.gl/pK7B0z#)
2.23 | 4 | 4 | 92290A228 | 5mm x 12mm SST socket head cap screw | $7.72 / 25 (http://goo.gl/sz4GxB#)
2.24 | 2 | 2 | HFS5-2020-567.5 | 20x20x567.5mm Extruded Aluminum | $15.00 / 1500mm | $3.23 (http://goo.gl/diXDGm#)
2.25 | 2 | 2 | HFS5-2020-218 | 20x20x218mm Extruded Aluminum | $15.00 / 1500mm | $3.03 (http://goo.gl/40MdnV#)
2.26 | 2 | 2 | HSCA5-R_170mm | T-SLot Covers (To Hold Clear Panels) | $3.00 / 1000mm (http://goo.gl/pXWmzj#) | $2.38 / 2000mm (http://goo.gl/ah7sAE#)
2.27 | 2 | 2 | HSCA5-R_537.5mm | T-SLot Covers (To Hold Clear Panels) | $3.00 / 1000mm (http://goo.gl/pXWmzj#) | $2.38 / 2000mm (http://goo.gl/ah7sAE#)
3 | 1 | | Front_Door (Optional, Subassembly)
3.1 | 2 | 2 | HFS5-2020-407.5 | 20x20x407.5mm Extruded Aluminum | $10.00 / 1000mm (http://goo.gl/Rn3xYc#) | $2.32 (http://goo.gl/vO8C3L#)
3.2 | 2 | 2 | HFS5-2020-567.5 | 20x20x567.5mm Extruded Aluminum | $10.00 / 1000mm (http://goo.gl/Rn3xYc#) | $3.23 (http://goo.gl/JglpGA#)
3.3 | 2 | 2 | HHPSN5 | Hinge for 20x20 Extrusion | $5.60 (http://goo.gl/a2ZCKD#)
3.4 | 8 | 8 | HNTTSN5-5 | T-Slot Nuts | $0.20 (http://goo.gl/D3hXRs#) | $28.00 / 100 (http://goo.gl/rpT76t#)
3.5 | 2 | 2 | HSCA5-R_537.5mm | T-SLot Covers (To Hold Clear Panels) | $3.00 / 1000mm (http://goo.gl/pXWmzj#) | $2.38 / 2000mm (http://goo.gl/ah7sAE#)
3.6 | 2 | 2 | HSCA5-R_407.5mm | T-SLot Covers (To Hold Clear Panels) | $3.00 / 1000mm (http://goo.gl/pXWmzj#) | $2.38 / 2000mm (http://goo.gl/ah7sAE#)
3.7 | 1 | 1 | .177in thick Acrylic_or_Polycarbonate_Door_Window | http://goo.gl/HMq1ng (http://goo.gl/HMq1ng#) | $15.70 (24"x24") (http://goo.gl/vB65Mp#)
3.8 | 8 | 8 | 91294A207 | 5mm x 8mm flat head socket cap screw | $6.75 / 100 (http://goo.gl/qvo2ic#)
3.9 | 4 | 4 | 91239A224 | 5mm x 10mm button head socket cap screw | $7.93 / 100 (http://goo.gl/gNzWFp#)
4 | 1 | | Power Supply (Subassembly)
4.1 | 1 | 1 | Meanwell_SE-450-24 | 24V 450W Power Supply (Lower Watt Version can be used with 120V bed) | $64.95 (http://goo.gl/5nyUF0#) | 39.99 (http://goo.gl/Z27x0m#)
4.2 | 1 | 1 | Power Supply Bracket 1 | 3D Printed | NA (http://goo.gl/5r42DL#)
4.3 | 2 | 2 | Power Supply Bracket 2 | 3D Printed | NA (http://goo.gl/ULRoFa#)
5 | 1 | | Electronics_Package (Subassembly)
5.1 | 1 | 1 | Q24169PCDCC | Hoffman Qline Enclosure (233x153x84mm) | $58.34 (http://goo.gl/HeFKDr#) | $58.41 (http://goo.gl/lhdL1U#)
5.2 | 1 | 1 | Hinge(McMaster_1598A180) | Hinge top swing electronics out of the way | $1.83 (http://goo.gl/samFHq#)
5.3 | 1 | 1 | Azteeg X3 V2 | Printer Controler Board | $174.99 w/ stepper (http://goo.gl/TDH8Es#) | $109.99 or $41.99 (http://goo.gl/mX7uks#)
5.4 | 1 | 1 | raspberrypi_b+ | Raspberry Pi B+ Print Server (for octoprint / octopi) | $39.99 (http://goo.gl/M8ljYJ#)
5.5 | 1 | 1 | ViKi LCD | print controller lcd | $75.00 (http://goo.gl/g2gTAf#) | $12.99 (http://goo.gl/oBHaC7#)
5.6 | 2 | 2 | Jamicon_KF0410-01 | 40x40mm 24v fan | $2.95 (http://goo.gl/30EsWk#)
5.7 | 1 lot | 1 lot | Cable Sleaving | Cable Sleave to keep wiring clean | $1.99 / Meter (http://goo.gl/16TCgx#)
6 | 1 | | Outlet_And_Network_Mount
6.1 | 1 | 1 | Outlet_Switch_And_Network_Mount | 3D Printed | NA (http://goo.gl/1x9LiW#)
6.2 | 1 | 1 | Amazon_Electrical_Fused_Plug | Fuse & Power Socket 10A 250V 3 Pin IEC320 C14 | $3.01 (http://goo.gl/prHJHU#)
6.3 | 1 | 1 | CAT5 Tooless IDC Keystone Jack | Network Keystone Jack | $4.35 (http://goo.gl/3GG4E4#)
7 | 1 | | Solid State Relay (Subassembly)
7.1 | 1 | 1 | G3NA_220B | 20A DC to AC Solid State Relay (to run heated bed at 120C AC) | $27.32 (http://goo.gl/pDBFty#)
7.2 | 2 | 2 | HNTTSN5-5 | T-Slot Nuts | $0.20 (http://goo.gl/D3hXRs#) | $28.00 / 100 (http://goo.gl/rpT76t#)
7.3 | 2 | 2 | 91239A224 | 5mm x 10mm button head socket cap screw | $7.93 / 100 (http://goo.gl/gNzWFp#)
8 | 1 | | Y_Limit_Switch (Subassembly)
8.1 | 1 | 1 | XY_LimitSwitch_Mount_A | 3D Printed | NA (http://goo.gl/hbjzwd#)
8.2 | 1 | 1 | Micro Switch Button | NO / NC Limit Switch | $1.99 (http://goo.gl/jhgq95#) | $2.00 (http://goo.gl/MqeAx2#)
8.3 | 1 | 1 | HNTTSN5-5 | T-Slot Nuts | $0.20 (http://goo.gl/D3hXRs#) | $28.00 / 100 (http://goo.gl/rpT76t#)
8.4 | 2 | 2 | 94500A223 | 3mm x 10mm button head socket cap screw | $6.08 / 100 (http://goo.gl/fJ8lt3#)

8.5 | 1 | 1 | 91239A224 | 5mm x 10mm button head socket cap screw | $7.93 / 100 (http://goo.gl/gNzWFp#)
9 | 1 | | X_Limit_Switch (Subassembly)
9.1 | 1 | 1 | XY_LimitSwitch_Mount_B | 3D Printed | NA (http://goo.gl/5WjjMY#)
9.2 | 1 | 1 | Micro Switch Button | NO / NC Limit Switch | $1.99 (http://goo.gl/jhgq95#) | $2.00 (http://goo.gl/MqeAx2#)
9.3 | 1 | 1 | HNTTSN5-5 | T-Slot Nuts | $0.20 (http://goo.gl/D3hXRs#) | $28.00 / 100 (http://goo.gl/rpT76t#)
9.4 | 2 | 2 | 94500A223 | 3mm x 10mm button head socket cap screw | $6.08 / 100 (http://goo.gl/fJ8lt3#)
9.5 | 1 | 1 | 91239A224 | 5mm x 10mm button head socket cap screw | $7.93 / 100 (http://goo.gl/gNzWFp#)
10 | 2 | | Drive_Corner_Bracket_A (Subassembly)
10.1 | 1 | 2 | Corner_Bearing_Bracket_A | 3D Printed | NA (http://goo.gl/prVhCj#)
10.2 | 14 | 28 | HNTTSN5-5 | T-Slot Nuts | $0.20 (http://goo.gl/D3hXRs#) | $28.00 / 100 (http://goo.gl/rpT76t#)
10.3 | 2 | 4 | 5972K164 | 10mm x 22mm x 6mm (6900 series bearing) | $9.99 / 10 (http://goo.gl/LsrN3b#)
10.4 | 2 | 4 | 90214A422 | 10mmx16mmx0.5mm Shim | $11.73 / 10 (http://goo.gl/0UJUQC#)
10.5 | 14 | 28 | 91239A224 | 5mm x 10mm button head socket cap screw | $7.93 / 100 (http://goo.gl/gNzWFp#)
11 | 2 | | Drive_Corner_Bracket_B (Subassembly)
11.1 | 1 | 2 | Corner_Bearing_Bracket_B | 3D Printed | NA (http://goo.gl/iHr469#)
11.2 | 14 | 28 | HNTTSN5-5 | T-Slot Nuts | $0.20 (http://goo.gl/D3hXRs#) | $28.00 / 100 (http://goo.gl/rpT76t#)
11.3 | 2 | 4 | 5972K164 | 10mm x 22mm x 6mm (6900 series bearing) | $9.99 / 10 (http://goo.gl/LsrN3b#)
11.4 | 2 | 4 | 90214A422 | 10mmx16mmx0.5mm Shim | $11.73 / 10 (http://goo.gl/0UJUQC#)
11.5 | 14 | 28 | 91239A224 | 5mm x 10mm button head socket cap screw | $7.93 / 100 (http://goo.gl/gNzWFp#)
12 | 1 | | X/Y Gantry Rods (Subassembly)
12.1 | 4 | 4 | SFJ10-610 | 10mm x 610mm hardened precicion rods for x/y axis guides | $20.33 (http://goo.gl/4aNCiS#)
12.2 | 2 | 2 | SFJ10-512 | 10mm x 512mm hardened precicion rods for x/y overhead gantry | $15.10 (http://goo.gl/DrbHPm#)
13 | 2 | | XY_Axis_Belt_Tensioner_A
13.1 | 1 | 2 | XY Axis Belt Tensioner A | 3D Printed | NA (http://goo.gl/XWmsyS#)
13.2 | 1 | 2 | XY Axis Belt Tensioner Block A | 3D Printed | NA (http://goo.gl/aQ1O2O#)
13.3 | 2 | 4 | a_7z41mpsb10m | 10mm self aligning bronze sintered bushings | $9.99 / 4 (http://goo.gl/KxiXtF#)
13.4 | 2 | 4 | 91290A137 | 3mm x 50mm socket head cap screw | $3.34 / 25 (http://goo.gl/jX49fs#)
13.5 | 4 | 8 | 90576A102 | 3mm nylock hex nut | $3.27 / 100 (http://goo.gl/MrPJOE#)
13.6 | 1 | 2 | 90591A146 | 3mm standard hex nut (DIN 934) | $2.08 / 100 (http://goo.gl/RTMkVX#)
13.7 | 1 | 2 | 91239A232 | 5mm x 16mm button head socket cap screw | $8.82 / 100 (http://goo.gl/eUfPl8#)
13.8 | 2 | 4 | 91290A125 | 3mm x 25mm socket head cap screw | $11.74 / 100 (http://goo.gl/k4jx9r#)
14 | 2 | | XY_Axis_Belt_Tensioner_B
14.1 | 1 | 2 | XY Axis Belt Tensioner B | 3D Printed | NA (http://goo.gl/NhKrEt#)
14.2 | 1 | 2 | XY Axis Belt Tensioner Block B | 3D Printed | NA (http://goo.gl/zTQV4N#)
14.3 | 2 | 4 | a_7z41mpsb10m | 10mm self aligning bronze sintered bushings | $9.99 / 4 (http://goo.gl/KxiXtF#)
14.4 | 2 | 4 | 91290A137 | 3mm x 50mm socket head cap screw | $3.34 / 25 (http://goo.gl/jX49fs#)
14.5 | 4 | 8 | 90576A102 | 3mm nylock hex nut | $3.27 / 100 (http://goo.gl/MrPJOE#)
14.6 | 1 | 2 | 90591A146 | 3mm standard hex nut (DIN 934) | $2.08 / 100 (http://goo.gl/RTMkVX#)
14.7 | 1 | 2 | 91239A232 | 5mm x 16mm button head socket cap screw | $8.82 / 100 (http://goo.gl/eUfPl8#)
14.8 | 2 | 4 | 91290A125 | 3mm x 25mm socket head cap screw | $11.74 / 100 (http://goo.gl/k4jx9r#)
15 | 1 | | XY Gantry Belts and Pullies
15.1 | 10 | 10 | GT2_Aluminum_Timing_Pulley_32_Tooth | GT2 2mm pitch, 10mm ID, 32 tooth pulley | $2.10 (http://goo.gl/CZc1Mn#)
15.2 | 5 | 5 | Bulk GT2 (2MM pitch x 6mm wide) Belt | Bulk GT2 (2MM pitch x 6mm wide) Belt | $1.8 / Meter (http://goo.gl/EfaApJ#) | $2 / meter (http://goo.gl/qtuN6B#)
15.3 | 2 | 2 | A 6R51M113060 | 113 tooth (226mm long) closed loop GT2 Belt (2mm pitch x 6mm wide) | $0.50 (http://goo.gl/Zq0XJU#) | $4.86 (http://goo.gl/0qO57G#)
16 | 2 | | X/Y Gantry Drive Motor (Subassembly)
16.1 | 1 | 2 | External_Motor | 3D Printed | NA (http://goo.gl/Cq2Ww3#)
16.2 | 1 | 2 | NEMA_17_60mm_1.5A | High Torque 6.5kg/cm 60mm Long Nema 17 Stepper Motor | $11.80 (http://goo.gl/KA4bML#)
16.3 | 4 | 8 | 91290A137 | 3mm x 50mm socket head cap screw | $3.34 / 25 (http://goo.gl/jX49fs#)
16.4 | 4 | 8 | HNTTSN5-5 | T-Slot Nuts | $0.20 (http://goo.gl/D3hXRs#) | $28.00 / 100 (http://goo.gl/rpT76t#)
16.5 | 1 | 2 | GT2_Aluminum_Timing_Pulley_20_Tooth | 20 tooth GT2 Pulley (5mm ID) (2mm pitch) | $1.85 (http://goo.gl/mr79RU#) | $5.49 (http://goo.gl/KOuMVZ#)
16.6 | 4 | 8 | 94500A223 | 3mm x 10mm button head socket cap screw | $6.08 / 100 (http://goo.gl/fJ8lt3#)
16.7 | 4 | 8 | 91239A224 | 5mm x 10mm button head socket cap screw | $7.93 / 100 (http://goo.gl/gNzWFp#)
17 | 1 | | Carriage_Dual_E3DV6
17.01 | 1 | 1 | Double Carriage_E3DV6 | 3D Printed | NA (http://goo.gl/a1HsP9#)
17.02 | 1 | 1 | Dual_Bowden_Tube_Carriage_Adapter_E3DV6 | 3D Printed | NA (http://goo.gl/WhGrAr#)
17.03 | 1 | 1 | Blower_Duct_1 | 3D Printed | NA (http://goo.gl/U2CrlK#)
17.04 | 1 | 1 | Blower_Duct_1Mirror | 3D Printed | NA (http://goo.gl/rOo9em#)
17.05 | 1 | 1 | Front_Clamp_With_Fan_Mount_E3DV6 | 3D Printed | NA (http://goo.gl/n3UiQN#)
17.06 | 1 | 1 | Dual_Fan_Shroud_E3DV6 | 3D Printed | NA (http://goo.gl/JHZzBV#)
17.07 | 4 | 4 | a_7z41mpsb10m | 10mm self aligning bronze sintered bushings | $9.99 / 4 (http://goo.gl/KxiXtF#)
17.08 | 2 | 2 | E3D_V6 | Hot End (need 24V fan and heater cartridge if 24V power supply is used, by default E3D V6 is designed for 12V system) | $79.99 (http://goo.gl/HCKlP8#)
17.09 | 2 | 2 | 50x50x15_Fonsoning_FSY5015S24H_Blower | 50x50x15 centrifugal blower fan (needs to be 24V if 24V power supply is used) | $6.81 (http://goo.gl/L2wzci#)
17.10 | 2 | 2 | 30x30_Fan | included with e3d kit (needs to be 24v if 24V power supply is used) | Request 24v when ordering (http://goo.gl/fpHrSM#)
17.11 | 11 | 11 | 90591A121 | 3mm hex nut (Din 934) | $1.39 / 100 (http://goo.gl/CRJEO4#)
17.12 | 4 | 4 | 92095A185 | 3mm x 20mm button head socket cap screw | $5.31 / 50 (http://goo.gl/jQcbs3#)
17.13 | 7 | 7 | 92095A184 | 3mm x 16mm button head socket cap screw | $8.85 / 100 (http://goo.gl/fRNg6u#)
17.14 | 2 | 2 | 91292A029 | 3mm x 18mm socket head cap screw | $5.60 / 100 (http://goo.gl/xjxiOO#)
17.15 | 2 | 2 | 91100A120 | 3mm oversized flat washer (Din 9021) | $1.10 / 100 (http://goo.gl/UicFWV#)
17.16 | 2 | 2 | 91292A123 | 3mm x 20mm socket head cap screw | $6.00 / 100 (http://goo.gl/CYRT7Y#)
18 | 2 | | Manual_Movement_Knob
18.1 | 1 | 2 | Rod_End_Knob | 3D Printed | NA (http://goo.gl/XC2qAD#)
18.2 | 1 | 2 | 90591A121 | 3mm hex nut (Din 934) | $1.39 / 100 (http://goo.gl/CRJEO4#)
18.3 | 1 | 2 | 94500A222 | 3mm x 8mm button head socket cap screw | $5.90 / 100 (http://goo.gl/1m2apX#)
19 | 1 | | Z_Bed_Assembly
19.1 | 2 | | Z_Axis_Module (Sub-Sub Assembly)
19.1.1 | 1 | 2 | MTSBRW12-480-F10-V8-S26-Q8 | 12mm Lead Screw 480L (both ends stepped to 8mm) | $51.25 (http://goo.gl/bLBkjn#) | $20.71 (http://goo.gl/HeSLzv#)
19.1.2 | 1 | 2 | Z_Leadscrew_Bearing_Holder_Top | 3D Printed | NA (http://goo.gl/AKLndV#)
19.1.3 | 1 | 2 | Z_Leadscrew_Bearing_ Holder_Base | 3D Printed | NA (http://goo.gl/c5zQRa#)
19.1.4 | 2 | 4 | 608ZZ-8x22x7 | 608ZZ Bearing | $0.90 (http://goo.gl/nH2HaR#) | $0.30 (http://goo.gl/dmeF2h#)
19.1.5 | 1 | 2 | GT2_Aluminum_Timing _Pulley_36_Tooth | GT2 2mm pitch, 8mm ID, 36 tooth pulley | $2.50 (http://goo.gl/tZYswC#) | $11.95 (http://goo.gl/HQEaW9#)

19.1.6 | 2 | 4 | 91290A252 | 5mm x 25mm socket head cap screw | $7.24 / 50 (http://goo.gl/amwn7C#)
19.1.7 | 4 | 8 | HNTTSN5-5 | T-Slot Nuts | $0.20 (http://goo.gl/D3hXRs#) | $28.00 / 100 (http://goo.gl/rpT76t#)
19.1.8 | 2 | 4 | 91239A232 | 5mm x 16mm button head socket cap screw | $8.82 / 100 (http://goo.gl/6j8S8b#)
19.2 | 2 | | Z_Gantry_Angle_Plate (Sub-Sub Assembly)
19.2.1 | 1 | 2 | Z_Gantry_Plate | ASTM B221-08 6063-T52 Aluminum Architectural Unequal Leg Angle 3-1/2" x 1-1/4" x 1/8" | $8.88 (http://goo.gl/k5VosG#)
19.2.2 | 4 | 8 | Dual_V_Wheel_Bolt_Assembly | Open Builds V-slot wheel kit | $3.85 (http://goo.gl/8z2P6z#) | $3.85 (http://goo.gl/FlhjBD#)
19.2.3 | 4 | 8 | 1/4" Eccentric Spacer | 1/4" Eccentric Spacer | $2.00 (http://goo.gl/vy7Wru#) | $2.00 (http://goo.gl/GPwMXa#)
19.2.4 | 1 | 2 | MTSRN12 | 12mm / 2mm pitch lead screw nut | $25.95 (http://goo.gl/tBK61C#) | Not needed with ball screw
19.2.5 | 4 | 8 | HNTTSN5-5 | T-Slot Nuts | $0.20 (http://goo.gl/D3hXRs#) | $28.00 / 100 (http://goo.gl/rpT76t#)
19.2.6 | 4 | 8 | 94500A230 | 5mm x 8mm button head socket cap screw | $6.15 / 50 (http://goo.gl/exEVR6#)
19.2.7 | 2 | 4 | 91239A224 | 5mm x 10mm button head socket cap screw | $7.93 / 100 (http://goo.gl/gNzWFp#)
19.3 | 1 | | Heated_Bed_Assembly
19.3.01 | 1 | 1 | Aluminum_Build_Plate | 1/4" ASTM B209-10 5052-H32 Aluminum Plate | $32.07 (http://goo.gl/ObY3yX#)
19.3.02 | 1 | 1 | MDF_Insulator_Board | 3/4" MDF Insulator board from local hardware store | $11.97 (http://goo.gl/oX5g37#)
19.3.03 | 4 | 4 | 92125A219 | 5mm x 70mm flat head socket cap screw | $4.38 / 10 (http://goo.gl/Jj3EYT#)
19.3.04 | 4 | 4 | 9657K292 | Spring (0.75"L x 0.50"OD x 0.062"wire) | $8.38 / 6 (http://goo.gl/1G61Hd#)
19.3.05 | 14 | 14 | 91100A140 | 5mm oversized flat washer (DIN 9021) | $3.45 / 100 (http://goo.gl/m0eBLq#)
19.3.06 | 2 | 2 | 92125A220 | 5mm x 30mm flat head socket cap screw | $6.55 / 25 (http://goo.gl/N29hxM#)
19.3.07 | 6 | 6 | 94205A240 | 5mm nylock nut (DIN 985) | $6.09 / 50 (http://goo.gl/9L9uR2#)
19.3.08 | 4 | 4 | 94545A225 | 5mm wing nut (DIN 315) | $6.21 / 10 (http://goo.gl/5sStfA#)
19.3.09 | 1 | 1 | 380mmx380mm_800W_ 120V_Silicone_Heater(Alirubber) | AliRubber Custom Silicon Heated Bed (You can spec Voltage, Wattage, Size, Thermistor Location, Etc.) (http://alirubber.en.alibaba.com/#) | $34.30 + Shipping
19.3.10 | 1 | 1 | Window_Glass_420mm X 430mm | Window Glass 420mm X 430mm or Boro Glass | $5.00 (http://goo.gl/o8U7FJ#)
19.3.11 | 2 | 2 | Bed_Glass_Clip | 3D Printed | NA (http://goo.gl/3RKh22#)
19.3.12 | 2 | 2 | Bed_Glass_Clip_Mirror | 3D Printed | NA (http://goo.gl/wD97Wl#)
19.3.13 | 2 | 2 | HFS5-2020-519_5 | 20x20x519.5mm Extruded Aluminum | $15.00 / 1500mm (http://goo.gl/Rn3xYc#) | 2.95 (http://goo.gl/J0SWRW#)
19.4 | 1 | | Z_Limit_Assembly
19.4.1 | 1 | 1 | Limit Switch Mounting Bracket | Aluminum Limit Switch Mounting Bracket | $2.00 (http://goo.gl/7gUrjR#) | $2.00
19.4.2 | 1 | 1 | Micro Switch Button | NO / NC Limit Switch | $1.99 (http://goo.gl/jhgq95#) | $2.00 (http://goo.gl/MqeAx2#)
19.4.3 | 1 | 1 | HNTTSN5-5 | T-Slot Nuts | $0.20 (http://goo.gl/D3hXRs#) | $28.00 / 100 (http://goo.gl/rpT76t#)
19.4.4 | 2 | 2 | 94500A223 | 3mm x 10mm button head socket cap screw | $6.08 / 100 (http://goo.gl/fJ8lt3#)
19.4.5 | 2 | 2 | 93475A210 | 3mm flat washer (DIN 125) | $1.62 / 100 (http://goo.gl/7ib0Np#)
19.4.6 | 1 | 1 | 91239A224 | 5mm x 10mm button head socket cap screw | $7.93 / 100 (http://goo.gl/gNzWFp#)
20 | 1 | | Z_Drive_Mount_With_Nema17_60mm
20.1 | 1 | 1 | External_Motor | 3D Printed | NA (http://goo.gl/Cq2Ww3#)
20.2 | 1 | 1 | NEMA_17_60mm_1.5A | High Torque 6.5kg/cm 60mm Long Nema 17 Stepper Motor | $11.80 (http://goo.gl/KA4bML#)
20.3 | 4 | 4 | 91290A137 | 3mm x 50mm socket head cap screw | $3.34 / 25 (http://goo.gl/jX49fs#)
20.4 | 4 | 4 | HNTTSN5-5 | T-Slot Nuts | $0.20 (http://goo.gl/D3hXRs#) | $28.00 / 100 (http://goo.gl/rpT76t#)
20.5 | 1 | 1 | GT2_Aluminum_Timing_Pulley_20_Tooth | 20 tooth GT2 Pulley (5mm ID) (2mm pitch) | $1.85 (http://goo.gl/mr79RU#) | $5.49 (http://goo.gl/KOuMVZ#)
20.6 | 4 | 4 | 94500A223 | 3mm x 10mm button head socket cap screw | $6.08 / 100 (http://goo.gl/fJ8lt3#)
20.7 | 1 | 1 | Timing Belt GT2 Profile - 2mm pitch - 6mm wide 1164mm long | 1164mm Long GT2 (2mm pitch) (6mm wide) (1164mm Long) | $9.95 (http://goo.gl/dXXzoa#)
20.8 | 4 | 4 | 91239A224 | 5mm x 10mm button head socket cap screw | $7.93 / 100 (http://goo.gl/gNzWFp#)
21 | 2 | | Z_Belt_Idler
21.1 | 1 | 2 | Z_Idler_Slide_Support | 3D Printed | NA (http://goo.gl/E9v8aX#)
21.2 | 1 | 2 | Smooth_Idler_Pulley kit | GT2 Smooth Idler Pulley | $4.85 (http://goo.gl/MrPQT9#) | $4.85 (http://goo.gl/qDO7Sm#)
21.3 | 2 | 4 | HNTTSN5-5 | T-Slot Nuts | $0.20 (http://goo.gl/D3hXRs#) | $28.00 / 100 (http://goo.gl/rpT76t#)
21.4 | 1 | 2 | 91290A254 | 5mm x 30mm socket head cap screw | $7.87 / 50 (http://goo.gl/EPZ8vJ#)
21.5 | 1 | 2 | 91239A224 | 5mm x 10mm button head socket cap screw | $7.93 / 100 (http://goo.gl/gNzWFp#)
22 | 2 | | Spool_and_Holder
22.1 | 1 | 2 | Spool_Holder_Flange | 3D Printed | NA (http://goo.gl/ddnDQb#)
22.2 | 1 | 2 | 50mm_Threaded_Spool_Holder_Full_Round | 3D Printed | NA (http://goo.gl/ljzOBR#)
22.3 | 4 | 8 | HNTTSN5-5 | T-Slot Nuts | $0.20 (http://goo.gl/D3hXRs#) | $28.00 / 100 (http://goo.gl/rpT76t#)
22.4 | 4 | 8 | 91239A224 | 5mm x 10mm button head socket cap screw | $7.93 / 100 (http://goo.gl/gNzWFp#)
23 | 2 | | HercuStruder_V2 | (recommended alternative = Bondtech Extruder)
23.01 | 1 | 2 | HercuLien_Extruder_Base_V2 | 3D Printed | NA (http://goo.gl/qJoZKl#)
23.02 | 1 | 2 | HercuStruder_Bearing_Pivot | 3D Printed | NA (http://goo.gl/ELpiO0#)
23.03 | 1 | 2 | HercuStruder_Dogbone_Connector | 3D Printed | NA (http://goo.gl/GvHtW2#)
23.04 | 1 | 2 | HercuStruder_Pin | 3D Printed | NA (http://goo.gl/CnOaw9#)
23.05 | 2 | 4 | Bowden_Tube_Nut_Trap | 3D Printed | NA (http://goo.gl/dcQW99#)
23.06 | 2 | 4 | HNTTSN5-5 | T-Slot Nuts | $0.20 (http://goo.gl/D3hXRs#) | $28.00 / 100 (http://goo.gl/rpT76t#)
23.07 | 1 | 2 | 4mmODx2mmID_Teflon_Tube_Section | Teflon tube for extruder drive inlet and bowden tube from extruder to the carriage | $12.00 (http://goo.gl/5os3y8#)
23.08 | 1 | 2 | 608ZZ-8x22x7 | 608ZZ Bearing | $0.90 (http://goo.gl/nH2HaR#) | $0.30 (http://goo.gl/dmeF2h#)
23.09 | 1 | 2 | 8mm_Shaft_Hobb_Gear | Filament Drive Gear | $9.95 (http://goo.gl/fVi6FK#)
23.10 | 1 | 2 | NEMA_17_5.18_Planetary | 5.18:1 planetary reduced 40mm Long Nema 17 Stepper Motor | $30.00 (http://goo.gl/04cDCz#)
23.11 | 4 | 8 | 90591A121 | 3mm hex nut (Din 934) | $1.39 / 100 (http://goo.gl/CRJEO4#)
23.12 | 2 | 4 | 91290A137 | 3mm x 50mm socket head cap screw | $3.34 / 25 (http://goo.gl/emRhce#)
23.13 | 4 | 8 | 93475A210 | 3mm flat washer (DIN 125) | $1.62 / 100 (http://goo.gl/7ib0Np#)
23.14 | 2 | 4 | 91100A120 | 3mm oversized flat washer (Din 9021) | $1.10 / 100 (http://goo.gl/UicFWV#)
23.15 | 2 | 4 | 92095A183 | 3mm x 12mm button head socket cap screw | $4.00 / 100 (http://goo.gl/5K1mk6#)
23.16 | 4 | 8 | 94500A223 | 3mm x 10mm button head socket cap screw | $6.08 / 100 (http://goo.gl/fJ8lt3#)
23.17 | 2 | 4 | 91290A135 | 3mm x 35mm socket head cap screw | $9.07 / 50 (http://goo.gl/ab3q40#)
23.18 | 2 | 4 | 90576A102 | 3mm nylock hex nut | $3.27 / 100 (http://goo.gl/MrPJOE#)
23.19 | 2 | 4 | 91239A224 | 5mm x 10mm button head socket cap screw | $7.93 / 100 (http://goo.gl/gNzWFp#)
23.20 | 2 | 4 | 94150A335 | 4mm hex nut (DIN 934) | $3.42 / 50 (http://goo.gl/kgnhHe#)
23.21 | 2 | 4 | 9657K283 | Spring (0.75"L x 0.187" OD x 0.029" Wire) | $9.80 / 12 (http://goo.gl/5htTLV#)

Other good suppliers and resources for parts

Bolts: | http://www.trimcraftaviationrc.com/ (http://www.trimcraftaviationrc.com/#)
Extruder: | http://www.bondtech.se/
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

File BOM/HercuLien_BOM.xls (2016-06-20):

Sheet: Ordering Details (BOM by Vendor
Part# | Qty | Description | Cost/Each | Total Cost | Link
.177in thick Acrylic or Polycarbonate | 7 | .177in thick Acrylic or Polycarbonate | $15.70 | $109.90 | http://www.amazon.com/Lexan-Sheet-Polycarbonate-Thick-Nominal/dp/B00CAWRVJO
1/4" Eccentric Spacer | 8 | 1/4" Eccentric Spacer | $2.00 | $16.00
1078A311 | 3 | Plastic Handle | $3.76 | $11.28 | http://www.mcmaster.com/#cad-2d/=w7lpr0
30x30_Fan | 2 | included with e3d kit (needs to be 24v if 24V power supply is used) |  | $0.00
380mmx380mm_800W_ 120V_Silicone_Heater(Alirubber) | 1 | AliRubber Custom Silicon Heated Bed (You can spec Voltage, Wattage, Size, Thermistor Location, Etc.) | $34.30 | $34.30
4mmODx2mmID_Teflon_Tube_Section | 2 | Teflon tube for extruder drive inlet and bowden tube from extruder to the carriage | $12.00 | $24.00
50x50x15_Fonsoning_FSY5015S24H_Blower | 2 | 50x50x15 centrifugal blower fan (needs to be 24V if 24V power supply is used) | $6.81 | $13.62
5972K164 | 1 | 10mm x 22mm x 6mm (6900 series bearing) (10 pack) | $9.99 | $9.99 | http://www.fasteddybearings.com/10-units-10x22x6-rubber-sealed-bearing-6900-2rs/
608ZZ-8x22x7 | 6 | 608ZZ Bearing | $0.30 | $1.80
8mm_Shaft_Hobb_Gear | 2 | Filament Drive Gear | $9.95 | $19.90
90214A422 | 1 | 10mmx16mmx0.5mm Shim (10 pack) | $11.73 | $11.73
90576A102 | 1 | 3mm nylock hex nut (25 pack) | $0.44 | $0.44 | http://www.trimcraftaviationrc.com/index.php?_a=product&product_id=234
90591A121 | 2 | 3mm hex nut (Din 934) (25 pack) | $0.24 | $0.48 | http://www.trimcraftaviationrc.com/index.php?_a=product&product_id=133
90965A160 | 1 | 5mm stainless flat washer (25 pack) | $0.19 | $0.19 | http://www.trimcraftaviationrc.com/index.php?_a=product&product_id=231
91100A120 | 1 | 3mm oversized flat washer (Din 9021) (100 pack) | $1.10 | $1.10 | http://www.mcmaster.com/#91100a120/=w7kv5a
91100A140 | 1 | 5mm oversized flat washer (DIN 9021) (100 pack) | $3.45 | $3.45 | http://www.mcmaster.com/#91100a140/=w7kusz
91239A224 | 3 | 5mm x 10mm button head screw | $7.93 | $23.79 | http://www.mcmaster.com/#91239a224/=w7kw2c
91239A232 | 1 | 5mm x 16mm button head socket cap screw (25 pack) | $1.22 | $1.22 | http://www.trimcraftaviationrc.com/index.php?_a=product&product_id=52
91290A125 | 1 | 3mm x 25mm socket head cap screw (25 pack) | $0.89 | $0.89 | http://www.trimcraftaviationrc.com/index.php?_a=product&product_id=197
91290A135 | 1 | 3mm x 35mm socket head cap screw (25 pack) | $0.89 | $0.89 | http://www.trimcraftaviationrc.com/index.php?_a=product&product_id=194
91290A137 | 1 | 3mm x 50mm socket head cap screw (25 pack) | $3.34 | $3.34 | http://www.mcmaster.com/#91290a137/=w7l1at
91290A252 | 1 | 5mm x 25mm socket head cap screw (25 pack) | $1.91 | $1.91 | http://www.trimcraftaviationrc.com/index.php?_a=product&product_id=179
91290A254 | 1 | 5mm x 30mm socket head cap screw (12 pack) | $1.31 | $1.31 | http://www.trimcraftaviationrc.com/index.php?_a=product&product_id=180
91292A029 | 1 | 3mm x 18mm socket head cap screw (25 pack) | $0.89 | $0.89 | http://www.trimcraftaviationrc.com/index.php?_a=product&product_id=434
91292A123 | 1 | 3mm x 20mm socket head cap screw (25 pack) | $0.84 | $0.84 | http://www.trimcraftaviationrc.com/index.php?_a=product&product_id=170
91294A207 | 1 | 5mm x 8mm flat head socket cap screw (100 pack) | $6.57 | $6.57 | http://www.mcmaster.com/#91294a207/=w7lc9s
92095A183 | 1 | 3mm x 12mm button head socket cap screw (25 pack) | $0.77 | $0.77 | http://www.trimcraftaviationrc.com/index.php?_a=product&product_id=23
92095A184 | 1 | 3mm x 16mm button head socket cap screw (25 pack) | $0.83 | $0.83 | http://www.trimcraftaviationrc.com/index.php?_a=product&product_id=26
92095A185 | 1 | 3mm x 20mm button head socket cap screw (25 pack) | $0.99 | $0.99 | http://www.trimcraftaviationrc.com/index.php?_a=product&product_id=27
92125A219 | 1 | 5mm x 70mm flat head socket cap screw (10 pack) | $4.38 | $4.38 | http://www.mcmaster.com/#92125a219/=w7lg57
92125A220 | 1 | 5mm x 30mm flat head socket cap screw (25 pack) | $6.55 | $6.55 | http://www.mcmaster.com/#92125a220/=w7lhvz
92290A228 | 1 | 5mm x 12mm SST socket head cap screw (25 pack) | $7.72 | $7.72 | http://www.mcmaster.com/#92290a228/=w7lj6a
93475A210 | 1 | 3mm flat washer (DIN 125) (25 pack) | $0.14 | $0.14 | http://www.trimcraftaviationrc.com/index.php?_a=product&product_id=230
94150A335 | 1 | 4mm hex nut (DIN 934) (25 pack) | $0.34 | $0.34 | http://www.trimcraftaviationrc.com/index.php?_a=product&product_id=134
94205A240 | 1 | 5mm nylock nut (DIN 985) (25 pack) | $0.66 | $0.66 | http://www.trimcraftaviationrc.com/index.php?_a=product&product_id=236
94500A222 | 1 | 3mm x 8mm button head socket cap screw (25 pack) | $0.52 | $0.52 | http://www.trimcraftaviationrc.com/index.php?_a=product&product_id=25
94500A223 | 2 | 3mm x 10mm button head socket cap screw (25 pack) | $0.64 | $1.28 | http://www.trimcraftaviationrc.com/index.php?_a=product&product_id=37
94500A230 | 1 | 5mm x 8mm button head socket cap screw (50 pack) | $6.15 | $6.15 | http://www.mcmaster.com/#94500a230/=w7lmba
94545A225 | 1 | 5mm wing nut (DIN 315) (10 pack) | $6.21 | $6.21 | http://www.mcmaster.com/#94545a225/=w7lnl4
9657K283 | 1 | Spring (0.75"L x 0.187" OD x 0.029" Wire) (12 pack) | $10.35 | $10.35 | http://www.mcmaster.com/#9657k283/=w7lo18
9657K292 | 1 | Spring (0.75"L x 0.50"OD x 0.062"wire) (6 pack) | $8.84 | $8.84 | http://www.mcmaster.com/#9657k292/=w7loha
A 6R51M113060 | 2 | 113 tooth (226mm long) closed loop GT2 Belt (2mm pitch x 6mm wide) | $0.50 | $1.00
a_7z41mpsb10m | 3 | 10mm self aligning bronze sintered bushings (4 pack) | $9.99 | $29.97
Aluminum_Build_Plate | 1 | 1/4" ASTM B209-10 5052-H32 Aluminum Plate | $32.07 | $32.07
Amazon_Electrical_Fused_Plug | 1 | Fuse & Power Socket 10A 250V 3 Pin IEC320 C14 | $3.01 | $3.01
Azteeg X3 V2 | 1 | Printer Controler Board | $174.99 | $174.99
Bulk GT2 (2MM pitch x 6mm wide) Belt | 5 | Bulk GT2 (2MM pitch x 6mm wide) Belt | $1.80 | $9.00
Cable Sleaving | 0 | Cable Sleave to keep wiring clean | $1.99 | $0.00
CAT5 Tooless IDC Keystone Jack | 1 | Network Keystone Jack | $4.35 | $4.35
Dual_V_Wheel_Bolt_Assembly | 8 | Open Builds V-slot wheel kit | $3.85 | $30.80
E3D_V6 | 2 | Hot End (need 24V fan and heater cartridge if 24V power supply is used, by default E3D V6 is designed for 12V system) | $79.99 | $159.98
G3NA_220B | 1 | 20A DC to AC Solid State Relay (to run heated bed at 120C AC) | $27.32 | $27.32
GT2_Aluminum_Timing _Pulley_36_Tooth | 2 | GT2 2mm pitch, 8mm ID, 36 tooth pulley | $2.50 | $5.00
GT2_Aluminum_Timing_Pulley_20_Tooth | 3 | 20 tooth GT2 Pulley (5mm ID) (2mm pitch) | $1.85 | $5.55
GT2_Aluminum_Timing_Pulley_32_Tooth | 10 | GT2 2mm pitch, 10mm ID, 32 tooth pulley | $2.10 | $21.00
HFC5-2020-B | 4 | Extrusion Endcap | $1.88 | $7.52
HFS5-2020-100 | 1 | 20x20x100mm Extruded Aluminum | $3.03 | $3.03
HFS5-2020-218 | 2 | 20x20x218mm Extruded Aluminum | $3.03 | $6.06
HFS5-2020-300 | 4 | 20x20x300mm Extruded Aluminum | $1.71 | $6.84
HFS5-2020-407.5 | 2 | 20x20x407.5mm Extruded Aluminum | $2.32 | $4.64
HFS5-2020-515 | 1 | 20x20x515mm Extruded Aluminum | $2.93 | $2.93
HFS5-2020-519_5 | 2 | 20x20x519.5mm Extruded Aluminum | 2.95 | $5.90
HFS5-2020-54.5 | 1 | 20x20x54.5mm Extruded Aluminum | $3.03 | $3.03
HFS5-2020-567.5 | 4 | 20x20x567.5mm Extruded Aluminum | $3.23 | $12.92
HFS5-2020-569.5 | 8 | 20x20x569.5mm Extruded Aluminum | $3.24 | $25.92
HFS5-2020-609.5 | 4 | 20mmx20mm609.5mm aluminum extrusion for vertical supports at the corners. Extrusions requires holes be drilled. 3d model for drill guide available. | $3.47 | $13.88
HFS5-2080-569.5 | 9 | 20x80x569.5mm aluminum extrusions. | $11.90 | $107.10
HHPSN5 | 6 | Hinge for 20x20 Extrusion | $5.60 | $33.60
Hinge(McMaster_1598A180) | 1 | Hinge top swing electronics out of the way | $1.83 | $1.83
HNTTSN5-5 (bag of 100) | 2 | T-Slot Nuts | $28.00 | $56.00
HSCA5-R (2M Lengths) | 12 | T-SLot Covers (To Hold Clear Panels) | $2.38 | $28.56
Jamicon_KF0410-01 | 2 | 40x40mm 24v fan | $2.95 | $5.90
Limit Switch Mounting Bracket | 1 | Aluminum Limit Switch Mounting Bracket | $2.00 | $2.00
MDF_Insulator_Board | 1 | 3/4" MDF Insulator board from local hardware store (Hand Routed) | $11.97 | $11.97
Meanwell_SE-450-24 | 1 | 24V 450W Power Supply (Lower Watt Version can be used with 120V bed) | $64.95 | $64.95
Micro Switch Button | 3 | NO / NC Limit Switch | $1.99 | $5.97
MTSBRW12-480-F10-V8-S26-Q8 | 2 | 12mm Lead Screw 480L (both ends stepped to 8mm) | $51.25 | $102.50 | Recommended to use ball screw at (http://goo.gl/HeSLzv) versus lead screw due to cost and speed of z-axis
MTSRN12 | 2 | 12mm / 2mm pitch lead screw nut | $25.95 | $51.90
NEMA_17_5.18_Planetary | 2 | 5.18:1 planetary reduced 40mm Long Nema 17 Stepper Motor | $30.00 | $60.00
NEMA_17_60mm_1.5A | 3 | High Torque 6.5kg/cm 60mm Long Nema 17 Stepper Motor | $11.80 | $35.40
Q24169PCDCC | 1 | Hoffman Qline Enclosure (233x153x84mm) | $58.34 | $58.34
raspberrypi_b+ | 1 | Raspberry Pi B+ Print Server (for octoprint / octopi) | $39.99 | $39.99
Rod_End_Knob | 2 | 3D Printed |  | $0.00
SFJ10-512 | 2 | 10mm x 512mm hardened precicion rods for x/y overhead gantry | $15.10 | $30.20
SFJ10-610 | 4 | 10mm x 610mm hardened precicion rods for x/y axis guides | $20.33 | $81.32
Smooth_Idler_Pulley kit | 2 | GT2 Smooth Idler Pulley | $4.85 | $9.70
Timing Belt GT2 Profile - 2mm pitch - 6mm wide 1164mm long | 1 | 1164mm Long GT2 (2mm pitch) (6mm wide) (1164mm Long) | $9.95 | $9.95
ViKi LCD | 1 | print controller lcd | $75.00 | $75.00
V-Slot_20mmX80mm489.5mm (1000mm cut in 2) | 1 | 20mmx80mmx489.5mm Vslot Extrusion | $10.00 | $10.00
Window_Glass_420mm X 430mm | 1 | Window Glass 420mm X 430mm or Boro Glass | $5.00 | $5.00
Z_Gantry_Plate | 2 | ASTM B221-08 6063-T52 Aluminum Architectural Unequal Leg Angle 3- 1/2" x 1-1/4" x 1/8" | $8.88 | $17.76
 |  |  | Total | $1857.21
Printed Parts | Qty:
Z_Idler_Slide_Support | 2
Z_Leadscrew_Bearing_ Holder_Base | 2
Z_Leadscrew_Bearing_Holder_Top | 2
Bed_Glass_Clip | 2
Bed_Glass_Clip_Mirror | 2
Blower_Duct_1 | 1
Blower_Duct_1Mirror | 1
Bowden_Tube_Nut_Trap | 4
Corner_Bearing_Bracket_A | 2
Corner_Bearing_Bracket_B | 2
Double Carriage_E3DV6 | 1
Dual_Bowden_Tube_Carriage_Adapter_E3DV6 | 1
Dual_Fan_Shroud_E3DV6 | 1
External_Motor | 3
Front_Clamp_With_Fan_Mount_E3DV6 | 1
HercuLien_Extruder_Base_V2 | 2
HercuStruder_Bearing_Pivot | 2
HercuStruder_Dogbone_Connector | 2
HercuStruder_Pin | 2
Outlet_Switch_And_Network_Mount | 1
Power Supply Bracket 1 | 1
Power Supply Bracket 2 | 2
Spool_Holder_Flange | 2
XY Axis Belt Tensioner A | 2
XY Axis Belt Tensioner B | 2
XY Axis Belt Tensioner Block A | 2
XY Axis Belt Tensioner Block B | 2
XY_LimitSwitch_Mount_A | 1
XY_LimitSwitch_Mount_B | 1
50mm_Threaded_Spool_Holder_Full_Round | 2

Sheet: Detailed BOM By Sub-Assembly
ITEM NO. | QTY. Per Subassembly | Qty Total | PART NUMBER | DESCRIPTION | Supplier 1: Links & Price ea. | Supplier 2: Links & Price ea.
1 | 1 |  | Herculien_Frame (Subassembly)
1.1 | 4 | 4 | HFS5-2020-609.5(holes_added) | 20mmx20mm609.5mm aluminum extrusion for vertical supports at the corners. Extrusions requires holes be drilled. 3d model for drill guide available. | $15.00 / 1500mm (http://goo.gl/Rn3xYc) | $3.47 (http://goo.gl/J2SwBg)
1.2 | 2 | 2 | HFS5-2080-569.5 (SidesBottom_Holes) | 20x80x569.5mm aluminum extrusions. | $30.00 / 1500mm (http://goo.gl/Rn3xYc) | $11.90 (http://goo.gl/2LajE3)
1.3 | 1 | 1 | HFS5-2080-569.5 (LeftTop_Holes) | 20x80x569.5mm aluminum extrusions. | $30.00 / 1500mm (http://goo.gl/Rn3xYc) | $11.90 (http://goo.gl/2LajE3)
1.4 | 1 | 1 | HFS5-2080-569.5 (RightTop_Holes) | 20x80x569.5mm aluminum extrusions. | $30.00 / 1500mm (http://goo.gl/Rn3xYc) | $11.90 (http://goo.gl/2LajE3)
1.5 | 3 | 3 | HFS5-2080-569.5 (Default_No Holes) | 20x80x569.5mm aluminum extrusions. | $30.00 / 1500mm (http://goo.gl/Rn3xYc) | $11.90 (http://goo.gl/2LajE3)
1.6 | 1 | 1 | HFS5-2080-569.5 (BackTop_Holes) | 20x80x569.5mm aluminum extrusions. | $30.00 / 1500mm (http://goo.gl/Rn3xYc) | $11.90 (http://goo.gl/2LajE3)
1.7 | 1 | 1 | HFS5-2080-569.5 (FrontTop_Holes) | 20x80x569.5mm aluminum extrusions. | $30.00 / 1500mm (http://goo.gl/Rn3xYc) | $11.90 (http://goo.gl/2LajE3)
1.8 | 2 | 2 | V-Slot_20mmX80mm489.5mm | 20mmx80mmx489.5mm Vslot Extrusion | $20.00 / 1000 (http://goo.gl/Rn3xYc) | $20.00 / 1000 (http://goo.gl/Sfh98b)
1.9 | 16 | 16 | HNTTSN5-5 | T-Slot Nuts | $0.20 (http://goo.gl/D3hXRs) | $28.00 / 100 (http://goo.gl/rpT76t)
1.1 | 6 | 6 | Optional: HSCA5-R_460mm | T-SLot Covers (To Hold Clear Panels) | $3.00 / 1000mm (http://goo.gl/pXWmzj) | $2.38 / 2000mm (http://goo.gl/ah7sAE)
1.11 | 6 | 6 | Optional: HSCA5-R_569.5mm | T-SLot Covers (To Hold Clear Panels) | $3.00 / 1000mm (http://goo.gl/pXWmzj) | $2.38 / 2000mm (http://goo.gl/ah7sAE)
1.12 | 1 | 1 | Optional: 4.3mm thick Acrylic_or_Polycarbonate_Rightside_Panel | http://goo.gl/oR3krK | $15.70 (24"x24") (http://goo.gl/vB65Mp)
1.13 | 1 | 1 | Optional: 4.3mm thick Acrylic_or_Polycarbonate_Leftside_Panel | http://goo.gl/YAD9aY | $15.70 (24"x24") (http://goo.gl/vB65Mp)
1.14 | 1 | 1 | Optional: 4.3mm thick Acrylic_or_Polycarbonate_Backside_Panel | http://goo.gl/BmHRNU | $15.70 (24"x24") (http://goo.gl/vB65Mp)
1.15 | 72 | 72 | 91239A224 | 5mm x 10mm button head screw | $7.93 / 100 (http://goo.gl/gNzWFp)
1.16 | 16 | 16 | 94500A230 | 5mm x 8mm button head socket cap screw | $6.15 / 50 (http://goo.gl/exEVR6)
2 | 1 |  | Top_Cover (Subassembly) (Optional, not needed for printer function)
2.1 | 3 | 3 | HFS5-2020-300 | 20x20x300mm Extruded Aluminum | $10.00 / 1000mm | $1.71 (http://goo.gl/0uMwHC)
2.2 | 1 | 1 | HFS5-2020-300 (configuration) | 20x20x300mm Extruded Aluminum | $10.00 / 1000mm (http://goo.gl/Rn3xYc) | $1.71 (http://goo.gl/uF3Bic)
2.3 | 8 | 8 | HFS5-2020-569.5 | 20x20x569.5mm Extruded Aluminum | $15.00 / 1500mm (http://goo.gl/Rn3xYc) | $3.24 (http://goo.gl/m5MVLF)
2.4 | 1 | 1 | HFS5-2020-515 | 20x20x515mm Extruded Aluminum | $15.00 / 1500mm | $2.93 (http://goo.gl/fW82FB)
2.5 | 1 | 1 | HFS5-2020-100 | 20x20x100mm Extruded Aluminum | from drop cut (http://goo.gl/Rn3xYc) | $3.03 (http://goo.gl/w7fIvp)
2.6 | 1 | 1 | HFS5-2020-54.5 | 20x20x54.5mm Extruded Aluminum | from drop cut (http://goo.gl/Rn3xYc) | $3.03 (http://goo.gl/BpjSgE)
2.7 | 4 | 4 | HHPSN5 | Hinge for 20x20 Extrusion | $5.60 (http://goo.gl/a2ZCKD)
2.8 | 20 | 20 | HNTTSN5-5 | T-Slot Nuts | $0.20 (http://goo.gl/D3hXRs) | $28.00 / 100 (http://goo.gl/rpT76t)
2.9 | 5 | 5 | HSCA5-R_300mm | T-SLot Covers (To Hold Clear Panels) | $3.00 / 1000mm (http://goo.gl/pXWmzj) | $2.38 / 2000mm (http://goo.gl/ah7sAE)
2.10 | 1 | 1 | HSCA5-R_515mm | T-SLot Covers (To Hold Clear Panels) | $3.00 / 1000mm (http://goo.gl/pXWmzj) | $2.38 / 2000mm (http://goo.gl/ah7sAE)
2.11 | 1 | 1 | HSCA5-R_98mm | T-SLot Covers (To Hold Clear Panels) | $3.00 / 1000mm (http://goo.gl/pXWmzj) | $2.38 / 2000mm (http://goo.gl/ah7sAE)
2.12 | 1 | 1 | HSCA5-R_48.5 | T-SLot Covers (To Hold Clear Panels) | $3.00 / 1000mm (http://goo.gl/pXWmzj) | $2.38 / 2000mm (http://goo.gl/ah7sAE)
2.13 | 1 | 1 | HSCA5-R_200mm | T-SLot Covers (To Hold Clear Panels) | $3.00 / 1000mm (http://goo.gl/pXWmzj) | $2.38 / 2000mm (http://goo.gl/ah7sAE)
2.14 | 11 | 11 | HSCA5-R_569.5mm | T-SLot Covers (To Hold Clear Panels) | $3.00 / 1000mm (http://goo.gl/pXWmzj) | $2.38 / 2000mm (http://goo.gl/ah7sAE)
2.15 | 4 | 4 | HFC5-2020-B | Extrusion Endcap | $1.88 (http://goo.gl/VBXGv2)
2.16 | 3 | 3 | .177in thick Acrylic or Polycarbonate Left Front Back Cover | http://goo.gl/mjZ4er | $15.70 (24"x24") (http://goo.gl/vB65Mp)
2.17 | 1 | 1 | .177in thick Acrylic or Polycarbonate Right Cover | http://goo.gl/rPAJGD | $15.70 (24"x24") (http://goo.gl/vB65Mp)
2.18 | 1 | 1 | .177in thick Acrylic or Polycarbonate Split Top Cover | http://goo.gl/l9hLrq | $15.70 (24"x24") (http://goo.gl/vB65Mp)
2.19 | 24 | 24 | 91239A224 | 5mm x 10mm button head socket cap screw | $7.93 / 100 (http://goo.gl/gNzWFp)
2.20 | 16 | 16 | 91294A207 | 5mm x 8mm flat head socket cap screw | $6.75 / 100 (http://goo.gl/qvo2ic)
2.21 | 2 | 2 | 1078A311 | Plastic Handle | $3.76 (http://goo.gl/qdXnO0)
2.22 | 2 | 2 | 90965A160 | 5mm stainless flat washer | $4.62 / 100 (http://goo.gl/pK7B0z)
2.23 | 4 | 4 | 92290A228 | 5mm x 12mm SST socket head cap screw | $7.72 / 25 (http://goo.gl/sz4GxB)
2.24 | 2 | 2 | HFS5-2020-567.5 | 20x20x567.5mm Extruded Aluminum | $15.00 / 1500mm | $3.23 (http://goo.gl/diXDGm)
2.25 | 2 | 2 | HFS5-2020-218 | 20x20x218mm Extruded Aluminum | $15.00 / 1500mm | $3.03 (http://goo.gl/40MdnV)
2.26 | 2 | 2 | HSCA5-R_170mm | T-SLot Covers (To Hold Clear Panels) | $3.00 / 1000mm (http://goo.gl/pXWmzj) | $2.38 / 2000mm (http://goo.gl/ah7sAE)
2.27 | 2 | 2 | HSCA5-R_537.5mm | T-SLot Covers (To Hold Clear Panels) | $3.00 / 1000mm (http://goo.gl/pXWmzj) | $2.38 / 2000mm (http://goo.gl/ah7sAE)
3 | 1 |  | Front_Door (Optional, Subassembly)
3.1 | 2 | 2 | HFS5-2020-407.5 | 20x20x407.5mm Extruded Aluminum | $10.00 / 1000mm (http://goo.gl/Rn3xYc) | $2.32 (http://goo.gl/vO8C3L)
3.2 | 2 | 2 | HFS5-2020-567.5 | 20x20x567.5mm Extruded Aluminum | $10.00 / 1000mm (http://goo.gl/Rn3xYc) | $3.23 (http://goo.gl/JglpGA)
3.3 | 2 | 2 | HHPSN5 | Hinge for 20x20 Extrusion | $5.60 (http://goo.gl/a2ZCKD)
3.4 | 8 | 8 | HNTTSN5-5 | T-Slot Nuts | $0.20 (http://goo.gl/D3hXRs) | $28.00 / 100 (http://goo.gl/rpT76t)
3.5 | 2 | 2 | HSCA5-R_537.5mm | T-SLot Covers (To Hold Clear Panels) | $3.00 / 1000mm (http://goo.gl/pXWmzj) | $2.38 / 2000mm (http://goo.gl/ah7sAE)
3.6 | 2 | 2 | HSCA5-R_407.5mm | T-SLot Covers (To Hold Clear Panels) | $3.00 / 1000mm (http://goo.gl/pXWmzj) | $2.38 / 2000mm (http://goo.gl/ah7sAE)
3.7 | 1 | 1 | .177in thick Acrylic_or_Polycarbonate_Door_Window | http://goo.gl/HMq1ng | $15.70 (24"x24") (http://goo.gl/vB65Mp)
3.8 | 8 | 8 | 91294A207 | 5mm x 8mm flat head socket cap screw | $6.75 / 100 (http://goo.gl/qvo2ic)
3.9 | 4 | 4 | 91239A224 | 5mm x 10mm button head socket cap screw | $7.93 / 100 (http://goo.gl/gNzWFp)
4 | 1 |  | Power Supply (Subassembly)
4.1 | 1 | 1 | Meanwell_SE-450-24 | 24V 450W Power Supply (Lower Watt Version can be used with 120V bed) | $64.95 (http://goo.gl/5nyUF0) | 39.99 (http://goo.gl/Z27x0m)
4.2 | 1 | 1 | Power Supply Bracket 1 | 3D Printed | NA (http://goo.gl/5r42DL)
4.3 | 2 | 2 | Power Supply Bracket 2 | 3D Printed | NA (http://goo.gl/ULRoFa)
5 | 1 |  | Electronics_Package (Subassembly)
5.1 | 1 | 1 | Q24169PCDCC | Hoffman Qline Enclosure (233x153x84mm) | $58.34 (http://goo.gl/HeFKDr) | $58.41 (http://goo.gl/lhdL1U)
5.2 | 1 | 1 | Hinge(McMaster_1598A180) | Hinge top swing electronics out of the way | $1.83 (http://goo.gl/samFHq)
5.3 | 1 | 1 | Azteeg X3 V2 | Printer Controler Board | $174.99 w/ stepper drivers (http://goo.gl/TDH8Es) | $109.99 or $41.99 (http://goo.gl/mX7uks)
5.4 | 1 | 1 | raspberrypi_b+ | Raspberry Pi B+ Print Server (for octoprint / octopi) | $39.99 (http://goo.gl/M8ljYJ)
5.5 | 1 | 1 | ViKi LCD | print controller lcd | $75.00 (http://goo.gl/g2gTAf) | $12.99 (http://goo.gl/oBHaC7)
5.6 | 2 | 2 | Jamicon_KF0410-01 | 40x40mm 24v fan | $2.95 (http://goo.gl/30EsWk)
5.7 | 1 lot | 1 lot | Cable Sleaving | Cable Sleave to keep wiring clean | $1.99 / Meter (http://goo.gl/16TCgx)
6 | 1 |  | Outlet_And_Network_Mount (Subassembly)
6.1 | 1 | 1 | Outlet_Switch_And_Network_Mount | 3D Printed | NA (http://goo.gl/1x9LiW)
6.2 | 1 | 1 | Amazon_Electrical_Fused_Plug | Fuse & Power Socket 10A 250V 3 Pin IEC320 C14 | $3.01 (http://goo.gl/prHJHU)
6.3 | 1 | 1 | CAT5 Tooless IDC Keystone Jack | Network Keystone Jack | $4.35 (http://goo.gl/3GG4E4)
7 | 1 |  | Solid State Relay (Subassembly)
7.1 | 1 | 1 | G3NA_220B | 20A DC to AC Solid State Relay (to run heated bed at 120C AC) | $27.32 (http://goo.gl/pDBFty)
7.2 | 2 | 2 | HNTTSN5-5 | T-Slot Nuts | $0.20 (http://goo.gl/D3hXRs) | $28.00 / 100 (http://goo.gl/rpT76t)
7.3 | 2 | 2 | 91239A224 | 5mm x 10mm button head socket cap screw | $7.93 / 100 (http://goo.gl/gNzWFp)
8 | 1 |  | Y_Limit_Switch (Subassembly)
8.1 | 1 | 1 | XY_LimitSwitch_Mount_A | 3D Printed | NA (http://goo.gl/hbjzwd)
8.2 | 1 | 1 | Micro Switch Button | NO / NC Limit Switch | $1.99 (http://goo.gl/jhgq95) | $2.00 (http://goo.gl/MqeAx2)
8.3 | 1 | 1 | HNTTSN5-5 | T-Slot Nuts | $0.20 (http://goo.gl/D3hXRs) | $28.00 / 100 (http://goo.gl/rpT76t)
8.4 | 2 | 2 | 94500A223 | 3mm x 10mm button head socket cap screw | $6.08 / 100 (http://goo.gl/fJ8lt3)
8.5 | 1 | 1 | 91239A224 | 5mm x 10mm button head socket cap screw | $7.93 / 100 (http://goo.gl/gNzWFp)
9 | 1 |  | X_Limit_Switch (Subassembly)
9.1 | 1 | 1 | XY_LimitSwitch_Mount_B | 3D Printed | NA (http://goo.gl/5WjjMY)
9.2 | 1 | 1 | Micro Switch Button | NO / NC Limit Switch | $1.99 (http://goo.gl/jhgq95) | $2.00 (http://goo.gl/MqeAx2)
9.3 | 1 | 1 | HNTTSN5-5 | T-Slot Nuts | $0.20 (http://goo.gl/D3hXRs) | $28.00 / 100 (http://goo.gl/rpT76t)
9.4 | 2 | 2 | 94500A223 | 3mm x 10mm button head socket cap screw | $6.08 / 100 (http://goo.gl/fJ8lt3)
9.5 | 1 | 1 | 91239A224 | 5mm x 10mm button head socket cap screw | $7.93 / 100 (http://goo.gl/gNzWFp)
10 | 2 |  | Drive_Corner_Bracket_A (Subassembly)
10.1 | 1 | 2 | Corner_Bearing_Bracket_A | 3D Printed | NA (http://goo.gl/prVhCj)
10.2 | 14 | 28 | HNTTSN5-5 | T-Slot Nuts | $0.20 (http://goo.gl/D3hXRs) | $28.00 / 100 (http://goo.gl/rpT76t)
10.3 | 2 | 4 | 5972K164 | 10mm x 22mm x 6mm (6900 series bearing) | $9.99 / 10 (http://goo.gl/LsrN3b)
10.4 | 2 | 4 | 90214A422 | 10mmx16mmx0.5mm Shim | $11.73 / 10 (http://goo.gl/0UJUQC)
10.5 | 14 | 28 | 91239A224 | 5mm x 10mm button head socket cap screw | $7.93 / 100 (http://goo.gl/gNzWFp)
11 | 2 |  | Drive_Corner_Bracket_B (Subassembly)
11.1 | 1 | 2 | Corner_Bearing_Bracket_B | 3D Printed | NA (http://goo.gl/iHr469)
11.2 | 14 | 28 | HNTTSN5-5 | T-Slot Nuts | $0.20 (http://goo.gl/D3hXRs) | $28.00 / 100 (http://goo.gl/rpT76t)
11.3 | 2 | 4 | 5972K164 | 10mm x 22mm x 6mm (6900 series bearing) | $9.99 / 10 (http://goo.gl/LsrN3b)
11.4 | 2 | 4 | 90214A422 | 10mmx16mmx0.5mm Shim | $11.73 / 10 (http://goo.gl/0UJUQC)
11.5 | 14 | 28 | 91239A224 | 5mm x 10mm button head socket cap screw | $7.93 / 100 (http://goo.gl/gNzWFp)
12 | 1 |  | X/Y Gantry Rods (Subassembly)
12.1 | 4 | 4 | SFJ10-610 | 10mm x 610mm hardened precicion rods for x/y axis guides | $20.33 (http://goo.gl/4aNCiS)
12.2 | 2 | 2 | SFJ10-512 | 10mm x 512mm hardened precicion rods for x/y overhead gantry | $15.10 (http://goo.gl/DrbHPm)
13 | 2 |  | XY_Axis_Belt_Tensioner_A (Subassembly)
13.1 | 1 | 2 | XY Axis Belt Tensioner A | 3D Printed | NA (http://goo.gl/XWmsyS)
13.2 | 1 | 2 | XY Axis Belt Tensioner Block A | 3D Printed | NA (http://goo.gl/aQ1O2O)
13.3 | 2 | 4 | a_7z41mpsb10m | 10mm self aligning bronze sintered bushings | $9.99 / 4 (http://goo.gl/KxiXtF)
13.4 | 2 | 4 | 91290A137 | 3mm x 50mm socket head cap screw | $3.34 / 25 (http://goo.gl/jX49fs)
13.5 | 4 | 8 | 90576A102 | 3mm nylock hex nut | $3.27 / 100 (http://goo.gl/MrPJOE)
13.6 | 1 | 2 | 90591A146 | 3mm standard hex nut (DIN 934) | $2.08 / 100 (http://goo.gl/RTMkVX)
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

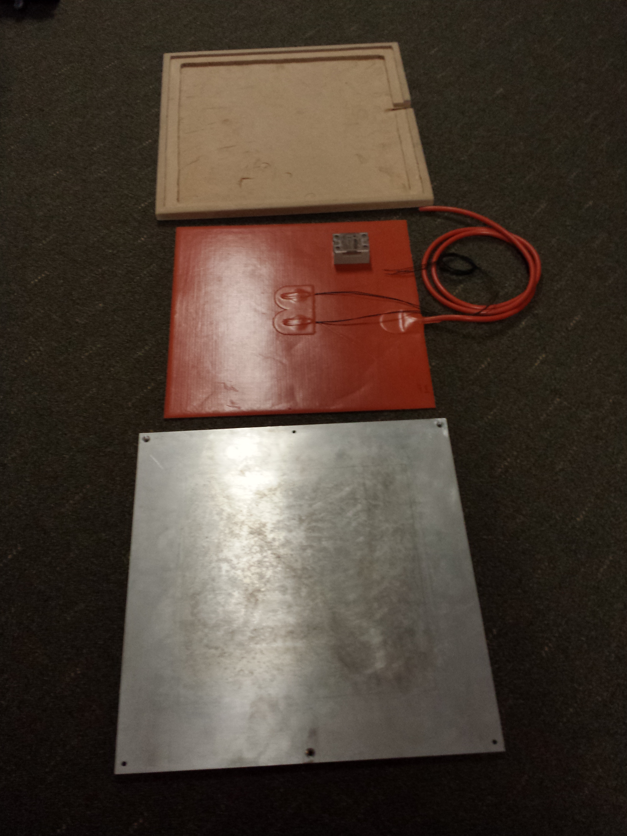
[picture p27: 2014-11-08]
Photos/Heated_Bed_Components.jpg

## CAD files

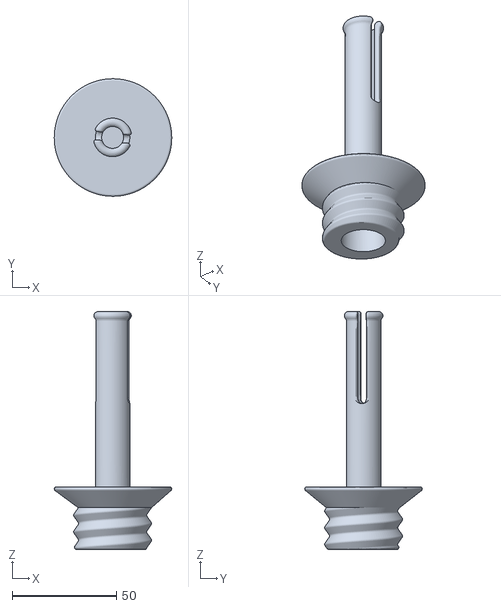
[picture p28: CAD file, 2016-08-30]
Community Mods and Upgrades/Zane Baird/Taulman_Threaded_Spool_Holder_Full_Round.stl
56.3 x 56.3 x 114.0

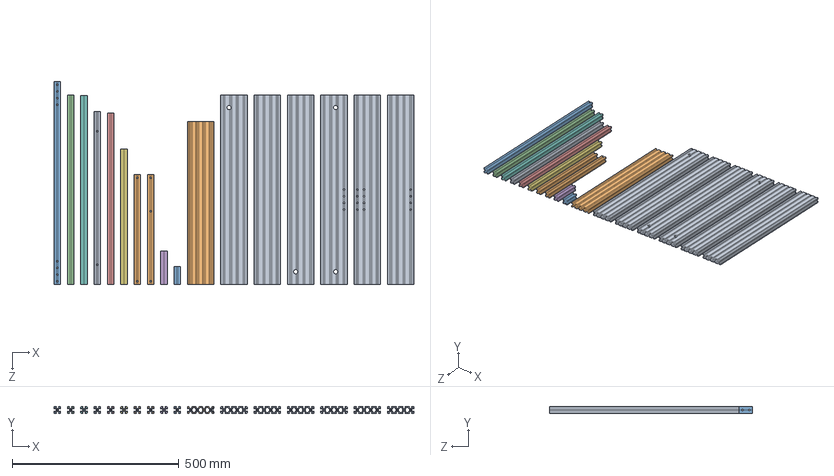
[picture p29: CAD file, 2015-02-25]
Documentation/Drawings/All_The_Extrusion_Pieces.SLDASM
1080.0 x 20.0 x 609.5 mm
HFS5-2020-519_5
HFS5-2020-330 x 2
HFS5-2020-54.5
HFS5-2020-569.5
HFS5-2020-515
HFS5-2020-100
HFS5-2020-407.5
HFS5-2020-567.5
HFS5-2080-569_5 x 6
V-Slot_20mmX80mm489.5mm
HFS5-2020-609_5(holes_added)

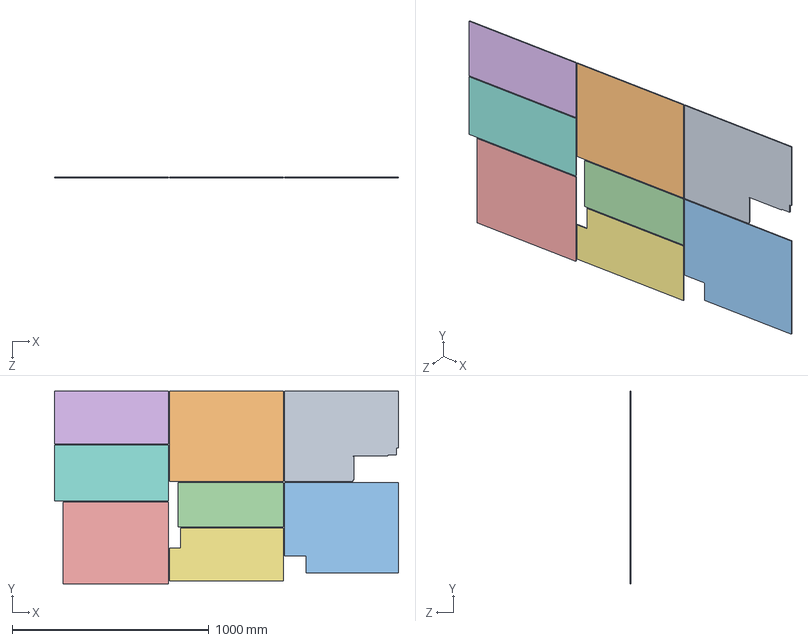
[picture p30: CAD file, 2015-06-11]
Documentation/Drawings/Panels/Panels.SLDASM
1747.0 x 978.8 x 4.50 mm
Acrylic_or_Polycarbonate_Backside_Panel
Acrylic_or_Polycarbonate_Leftside_Panel
Acrylic_or_Polycarbonate_Rightside_Panel
Acrylic_or_Polycarbonate_Cover_Door
Acrylic_or_Polycarbonate_Door_Window
Acrylic_or_Polycarbonate_Left_Front_Back_Cover
Acrylic_or_Polycarbonate_Right_Cover
Acrylic_or_Polycarbonate_SplitTop_Cover

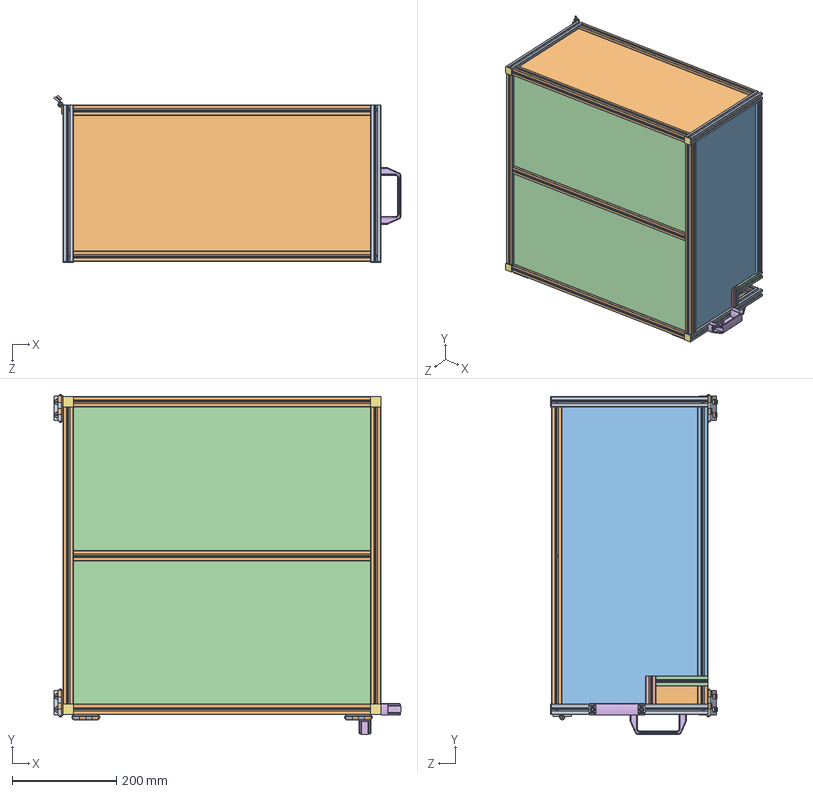
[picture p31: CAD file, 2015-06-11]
Sub Assemblies/Top_Cover.SLDASM
665.1 x 651.8 x 321.0 mm
HFS5-2020-300 x 4
HFS5-2020-569.5 x 6
HFS5-2020-515
HFS5-2020-100
HFS5-2020-54.5
HFS5-2020-567.5 x 2
HFS5-2020-218 x 2
HHPSN5-pin x 4
HHPSN5-l x 4
HHPSN5-r x 4
5mmX10mm_Buttonhead(McMaster_91239A224) x 24
5mmX8mm_Flathead(McMaster_91294A207) x 16
HNTTSN5-5 x 20
Handle_(McMaster_1078A311) x 2
5mm_Flatwasher(McMaster_90965A160) x 2
5mmX12mm_Sockethead(McMaster_92290A228) x 4
HSCA5-R_270mm x 5
HSCA5-R_515mm
HSCA5-R_98mm
HSCA5-R_48.5
HSCA5-R_170mm
HSCA5-R_569.5mm x 10
HFC5-2020-Bc x 4
HSCA5-R_537.5mm x 2
HSCA5-R_218mm x 2
Acrylic_or_Polycarbonate_Left_Front_Back_Cover x 2
Acrylic_or_Polycarbonate_Right_Cover
Acrylic_or_Polycarbonate_SplitTop_Cover x 2
Acrylic_or_Polycarbonate_Cover_Door

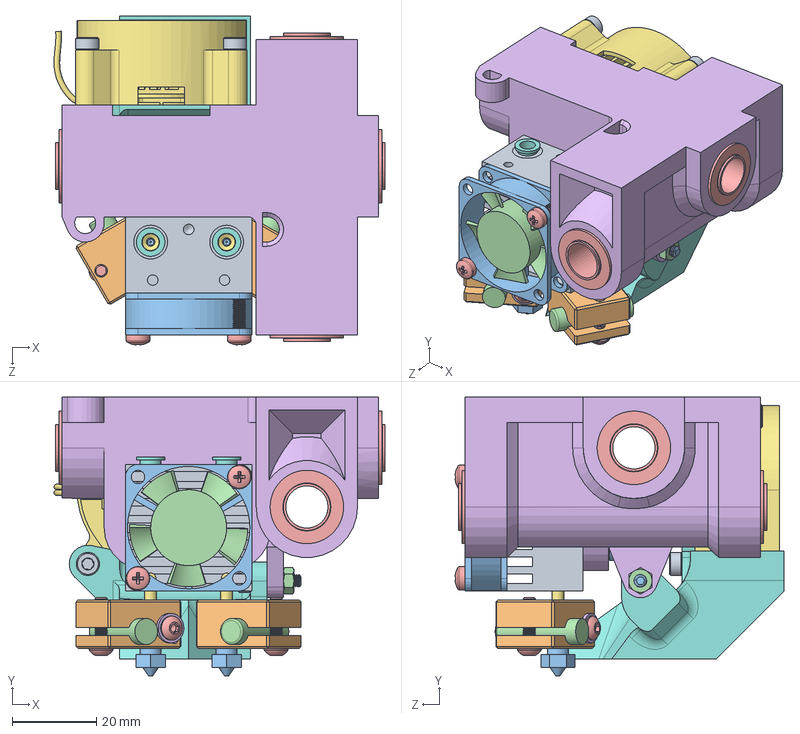
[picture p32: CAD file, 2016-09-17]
Community Mods and Upgrades/Eric Lien/HercuLien Eustathios Chimera Carriage/Solidworks/00 - Solidworks_Compact_Dual_Extruder.SLDASM
78.4 x 66.0 x 77.9 mm
Cyclops Heatsink
v6 Heat Block x 2
v6 Nozzle x 2
cartridge heater x 2
socket button head cap screw_am x 4
flat washer narrow_am x 2
Cyclops Heat Break x 2
v6 Coupling x 2
v6 Ferrule x 2
socket set screw oval point_am x 4
Fan-House-30x30x10-Promoco
Fan-30x30x10-Promoco
pan cross head_am x 2
Compact_Dual_Extruder
4020Blower
Part Cooling Duct
91292A123 x 3
92398A121 x 2
91292A114 x 4
94150A325 x 2
a_7z41mpsb10m x 4

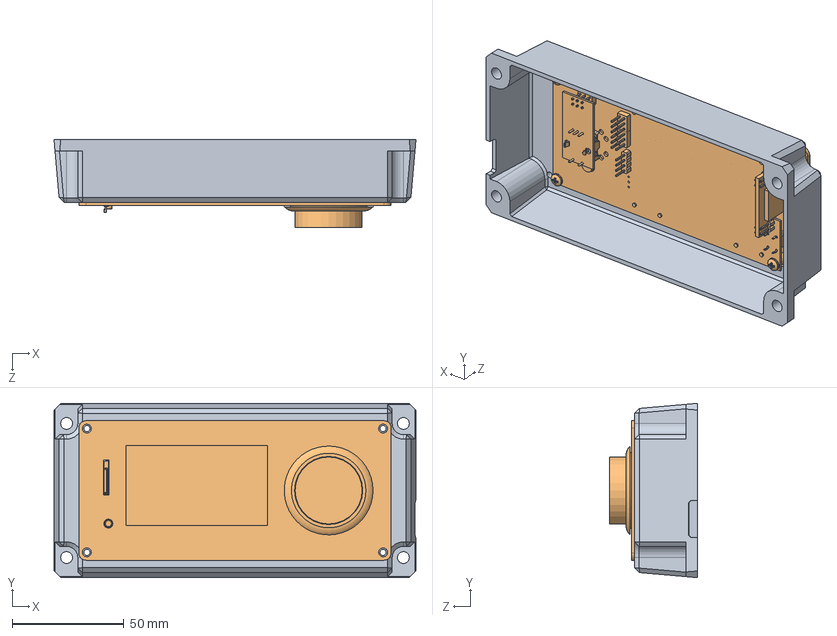
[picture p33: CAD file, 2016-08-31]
Community Mods and Upgrades/Eric Lien/Viki2 Front Mount/Viki2_Front_Mount_Assembly.SLDASM
162.0 x 78.0 x 39.2 mm
HercuLien_Viki2_Mount_Front_Face
Viki2_LCD

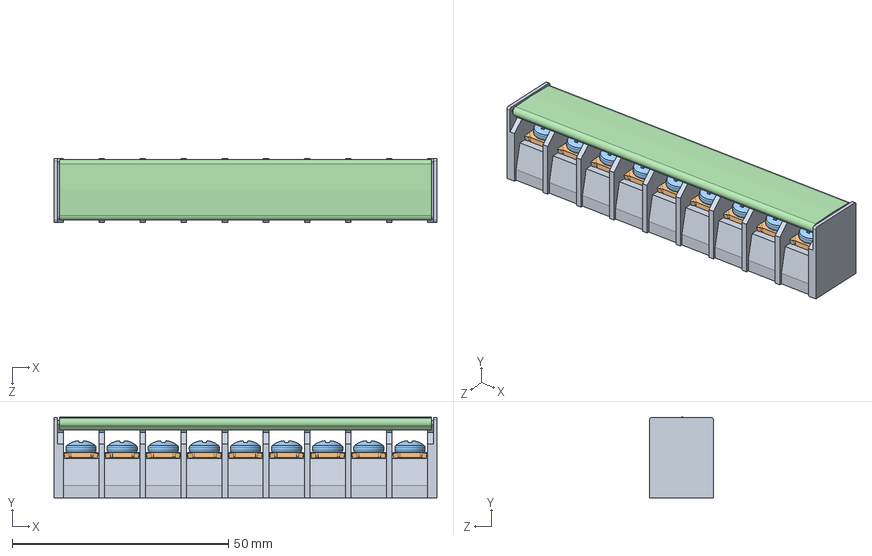
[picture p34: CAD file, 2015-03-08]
Electronics/Switchlab T14-EO33-09 Terminal Block.SLDASM
88.5 x 18.6 x 14.7 mm
Body of Switchlab T14-EO33-09 Terminal Block
Clamp Plate of Switchlab T14-EO33-09 Terminal Block x 9
Philips-Drive Panhead Screw of Switchlab T14-EO33-09 Terminal Block x 9
Cover for Switchlab T14-EO33-09 Terminal Block

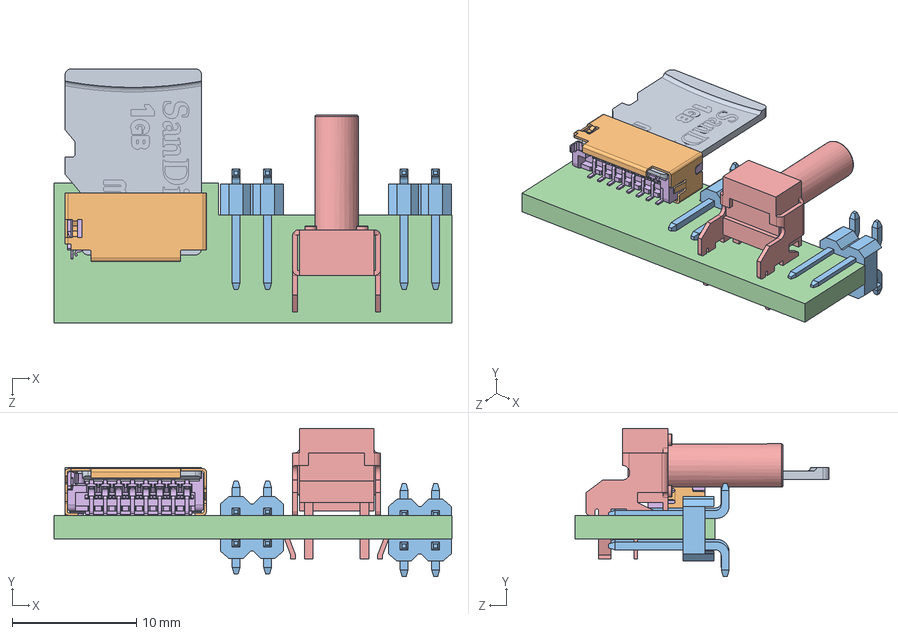
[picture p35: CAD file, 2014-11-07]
Electronics/Viki LCD/TF slot assm.sldasm
32.1 x 12.0 x 20.5 mm
User Library-Micro_SD
pin_header_a-sl254-dg-g04mp1 x 2
TF PCB
FSMRA7JH

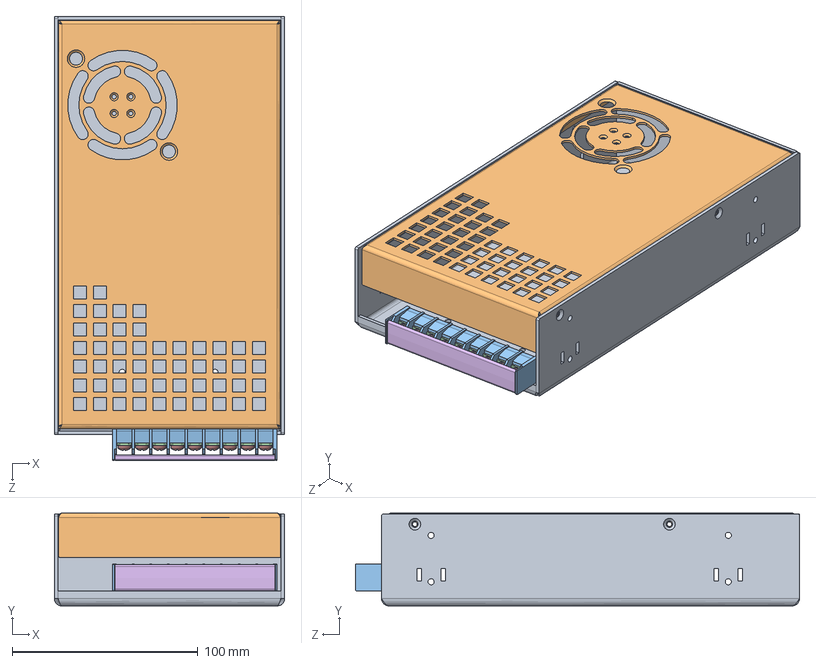
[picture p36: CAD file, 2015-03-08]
Sub Assemblies/Meanwell_SE-450-24.SLDASM
124.0 x 50.0 x 239.0 mm
Mean Well SE-450 Base
Mean Well SE-450 Top
Body of Switchlab T14-EO33-09 Terminal Block
Clamp Plate of Switchlab T14-EO33-09 Terminal Block x 9
Philips-Drive Panhead Screw of Switchlab T14-EO33-09 Terminal Block x 9
Cover for Switchlab T14-EO33-09 Terminal Block

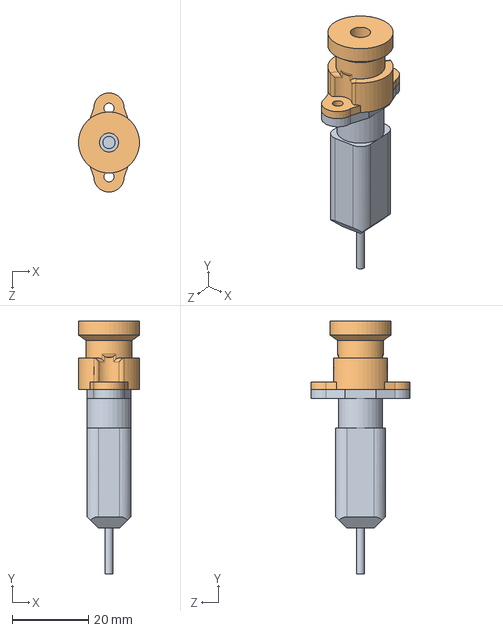
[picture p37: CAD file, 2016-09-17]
Community Mods and Upgrades/Eric Lien/BLTouch 2nd Hotend Mount/Adapter_With_BLTouch.SLDASM
16.0 x 66.3 x 26.0 mm
BLTouch
BLTouchAdapter_2nd_Hotend_Adapter

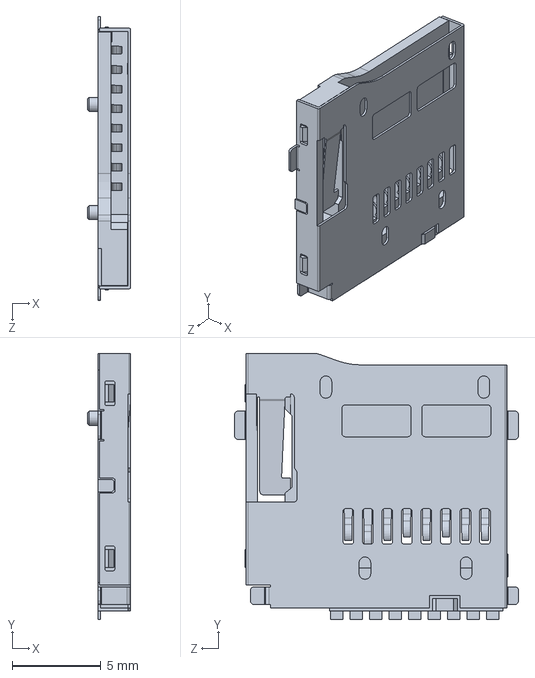
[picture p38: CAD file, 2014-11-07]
Electronics/Raspberry Pi B+/raspberry_pi_B+_(slot).SLDASM
2.44 x 15.0 x 16.0 mm

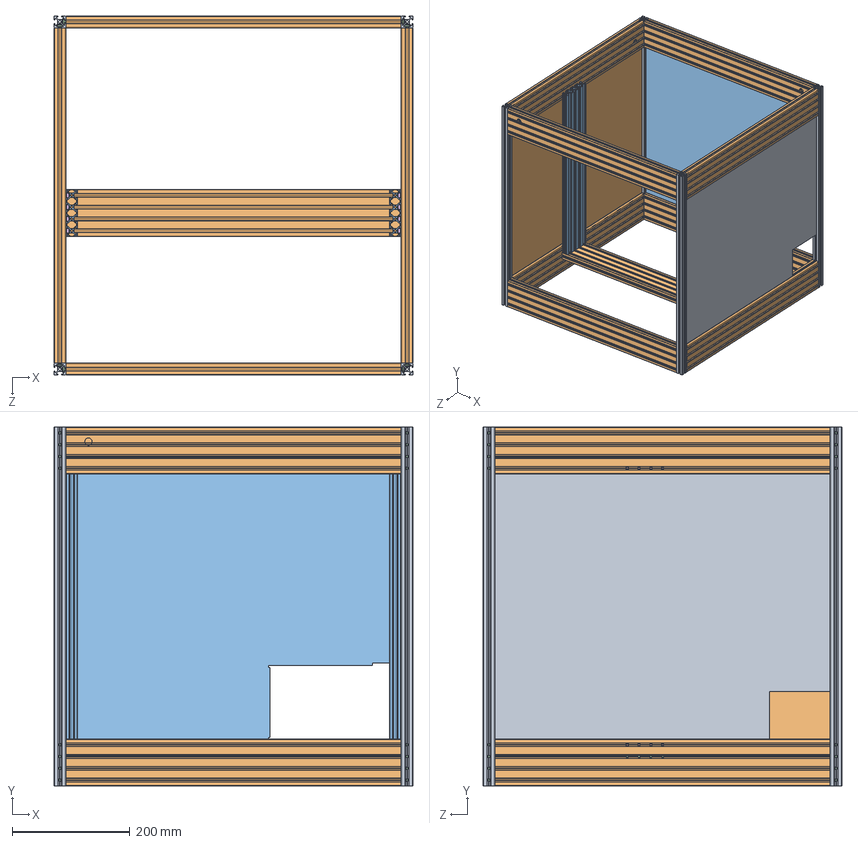
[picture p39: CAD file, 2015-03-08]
Sub Assemblies/Herculien_Frame.SLDASM
609.5 x 609.5 x 609.5 mm
HFS5-2020-609_5(holes_added) x 4
HFS5-2080-569_5 x 9
V-Slot_20mmX80mm489.5mm x 2
5mmX10mm_Buttonhead(McMaster_91239A224) x 72
5mmX8mm_Buttonhead(McMaster_94500A230) x 16
HNTTSN5-5 x 16
HSCA5-R_460mm x 6
HSCA5-R_569.5mm x 6
Acrylic_or_Polycarbonate_Rightside_Panel
Acrylic_or_Polycarbonate_Leftside_Panel
Acrylic_or_Polycarbonate_Backside_Panel

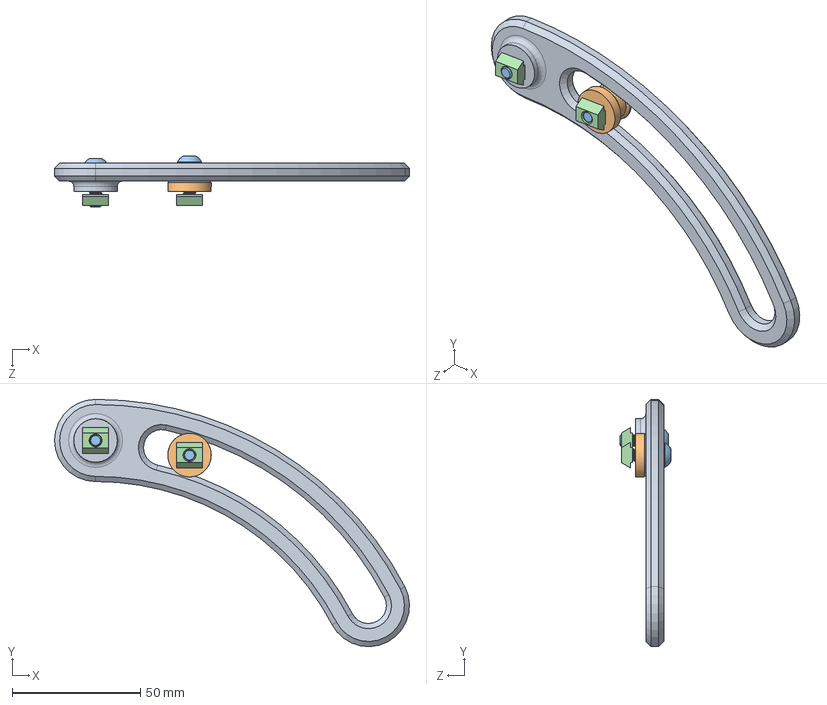
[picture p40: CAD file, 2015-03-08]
Sub Assemblies/Lid_Stop.SLDASM
138.3 x 96.3 x 19.8 mm
Lid_Stop
Lid_Stop_Peg
5mmX16mm_Buttonhead(McMaster_91239A232) x 2
HNTTSN5-5 x 2

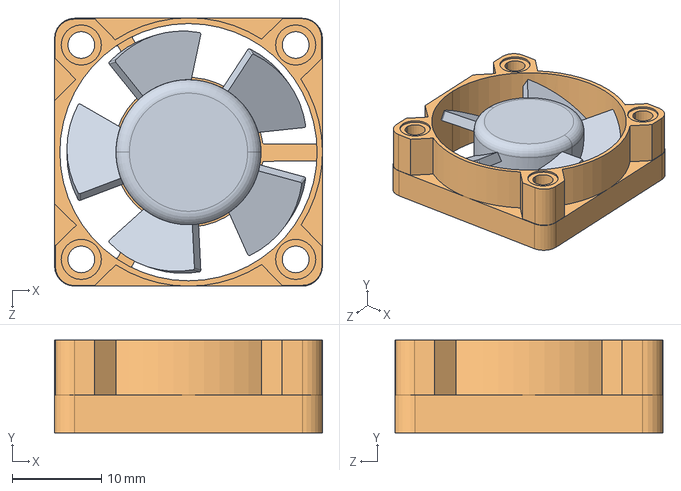
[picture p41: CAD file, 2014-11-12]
Electronics/30x30_Fan.SLDASM
30.0 x 10.4 x 30.0 mm
D3010_SOLID_1
D3010_QUILT_1

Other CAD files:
Electronics/Raspberry Pi B+/raspberry_pi_B+_(micro_USB).SLDASM
Electronics/Viki LCD/ViKi LCD.sldasm
Sub Assemblies/Front_Door.SLDASM
Sub Assemblies/Z_Gantry_Angle_Plate.SLDASM
Community Mods and Upgrades/Ashley Webster/151007 - XY end rod clamp - 3DPV rev A.stl
Community Mods and Upgrades/Ashley Webster/151007 - XY end snap bearing - 3DPV rev A.stl
Community Mods and Upgrades/Ashley Webster/151007 - XY end snap bearing - 3DPV rev A.stp
Community Mods and Upgrades/Ashley Webster/151007 - XY end tension blocks - 3DPV rev A.stl
Community Mods and Upgrades/Eric Lien/Azteeg X5 GT and RasPI Enclosure/Azteeg_X5_GT_Case.SLDPRT
Community Mods and Upgrades/Eric Lien/Azteeg X5 GT and RasPI Enclosure/Azteeg_X5_GT_Case.STEP
Community Mods and Upgrades/Eric Lien/Azteeg X5 GT and RasPI Enclosure/Azteeg_X5_GT_Case.x_t
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

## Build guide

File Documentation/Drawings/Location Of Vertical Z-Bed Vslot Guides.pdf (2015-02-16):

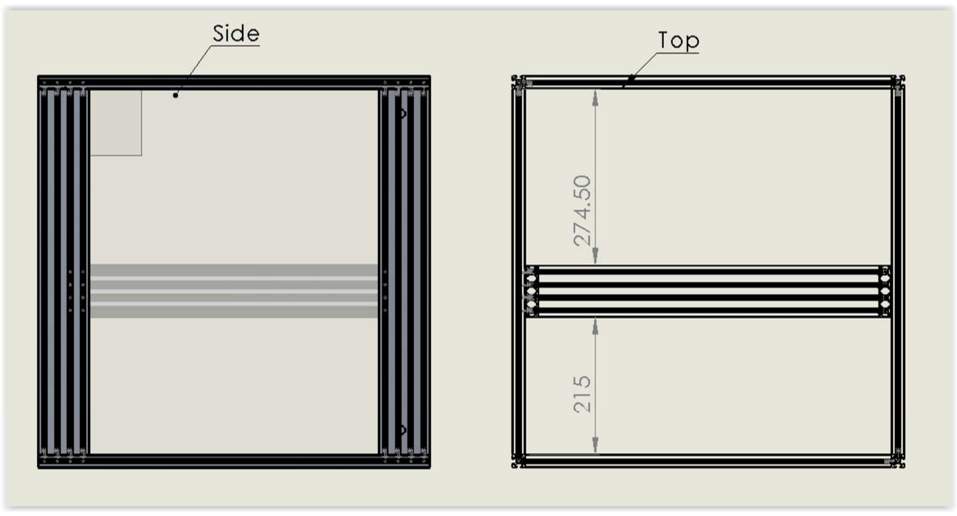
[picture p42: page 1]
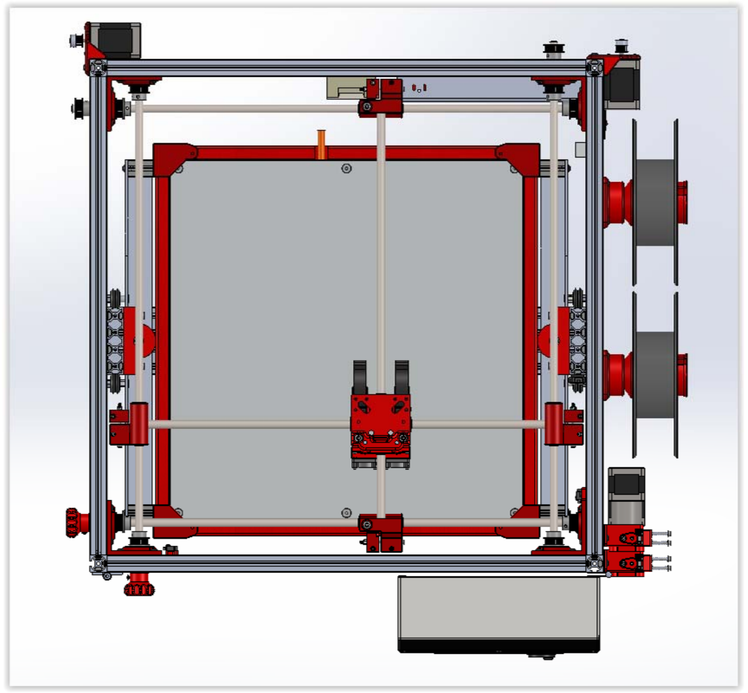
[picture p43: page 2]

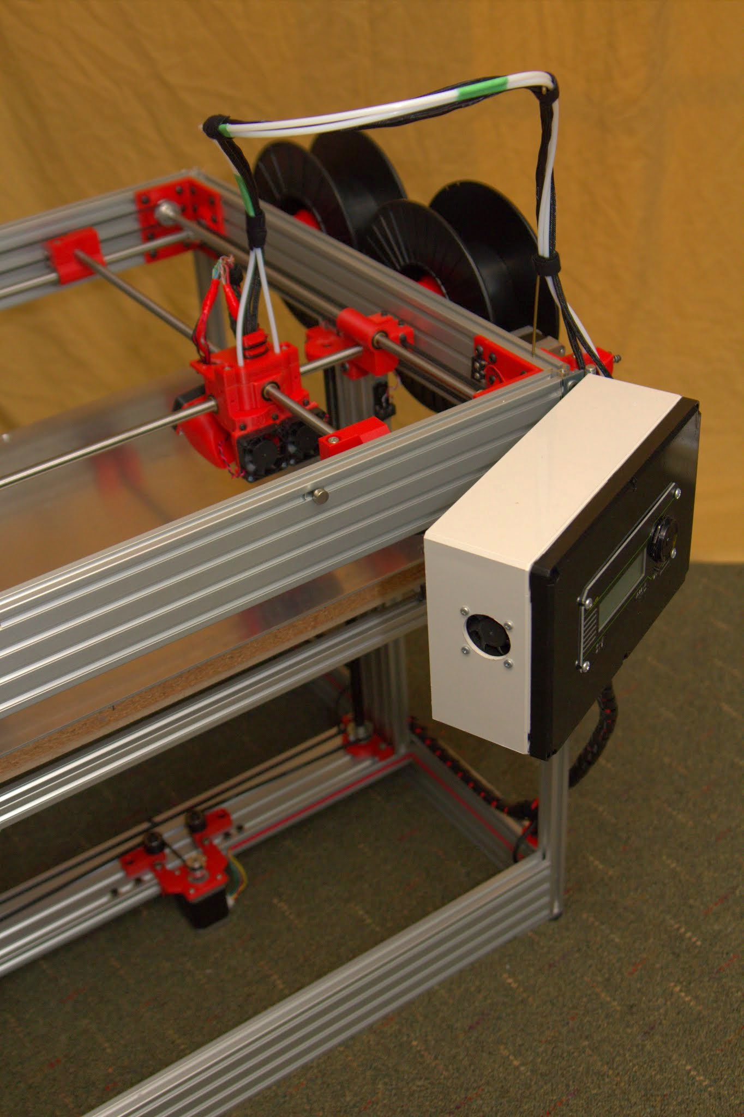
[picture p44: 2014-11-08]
Photos/Assembled_HercuLien (2).jpg

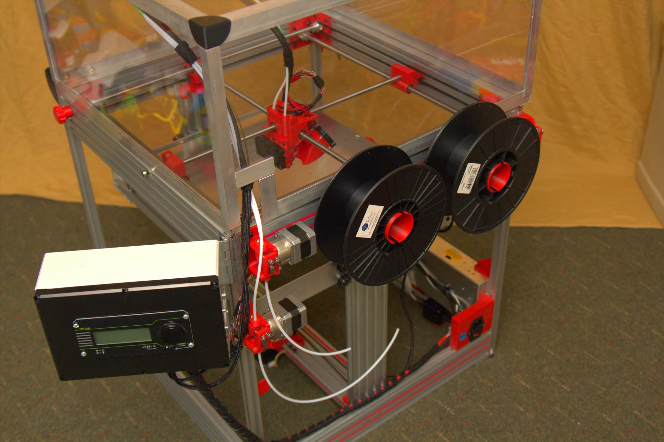
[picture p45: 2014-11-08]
Photos/Assembled_HercuLien (3).jpg

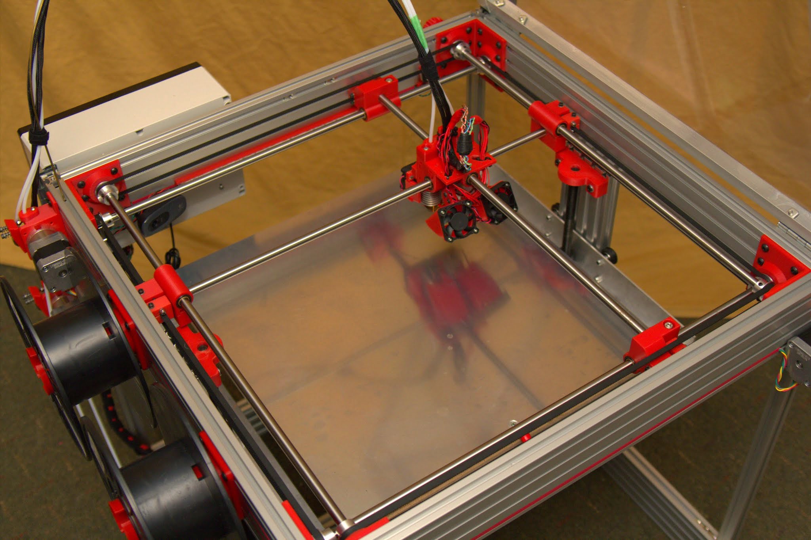
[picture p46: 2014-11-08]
Photos/Assembled_HercuLien (16).jpg

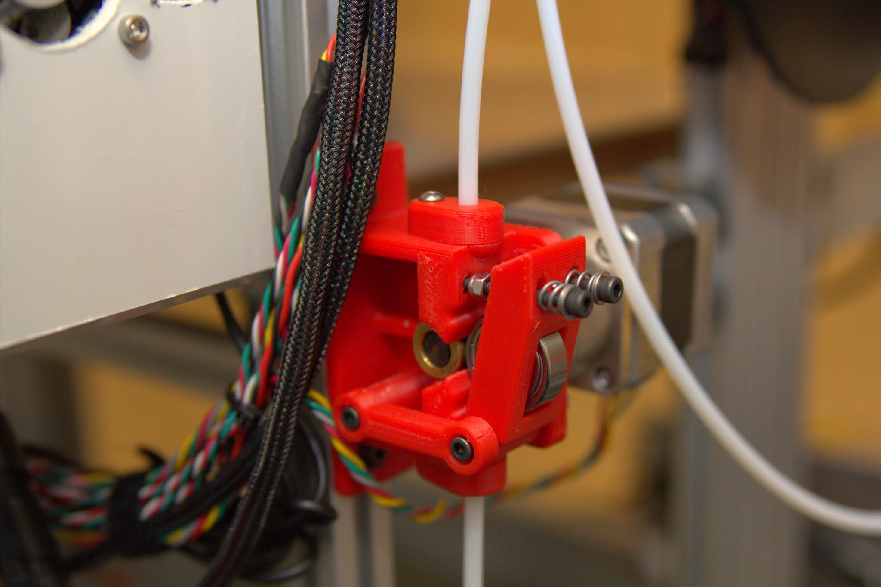
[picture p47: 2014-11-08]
Photos/Assembled_HercuLien (10).jpg

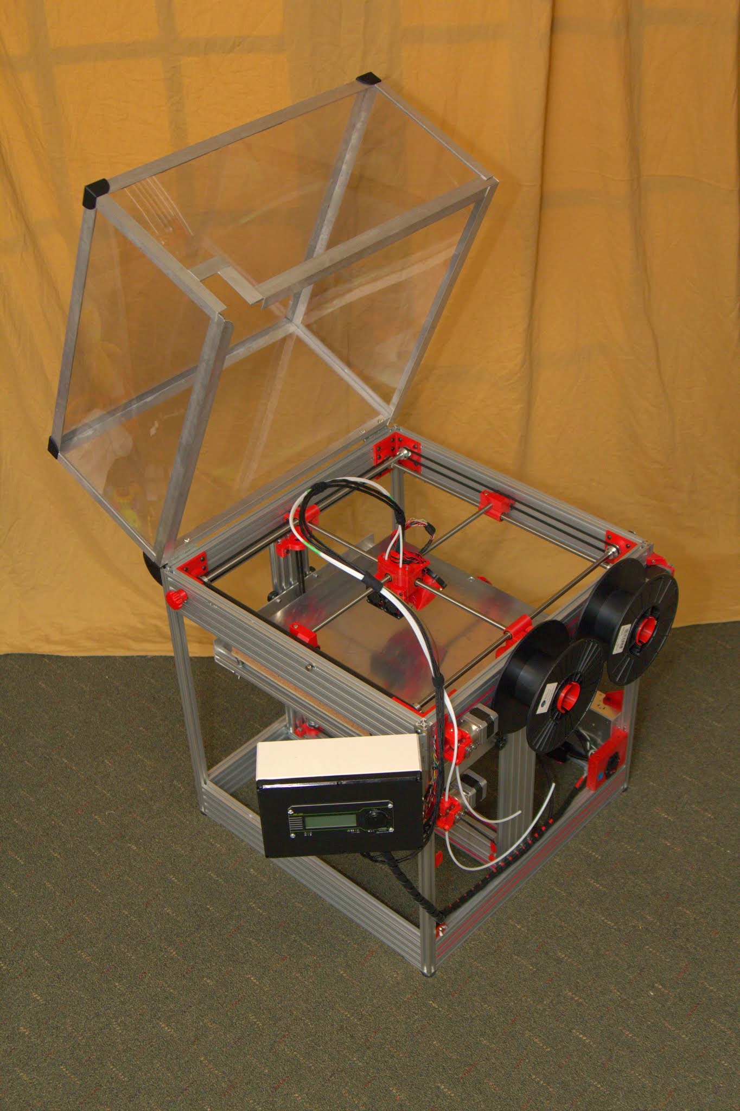
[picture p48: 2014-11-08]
Photos/Assembled_HercuLien (6).jpg

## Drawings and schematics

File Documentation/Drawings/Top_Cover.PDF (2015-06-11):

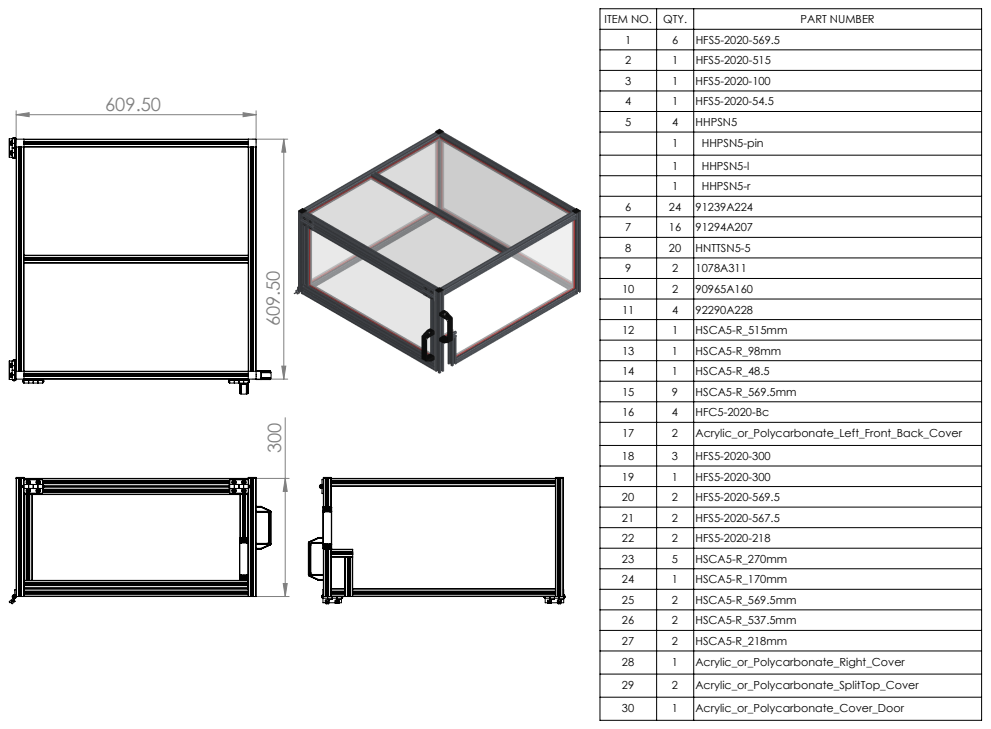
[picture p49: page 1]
ITEM NO.; QTY.; PART NUMBER 1; HFS5-2020-569.5 2; HFS5-2020-515 3; HFS5-2020-100 4; HFS5-2020-54.5 5; HHPSN5 1; HHPSN5-pin 1; HHPSN5-l 1; HHPSN5-r 6; HNTTSN5-5 9

10 | 2 | 90965A160
11 | 4 | 92290A228
12 | 1 | HSCA5-R_515mm
13 | 1 | HSCA5-R_98mm
14 | 1 | HSCA5-R_48.5
15 | 9 | HSCA5-R_569.5mm
16 | 4 | HFC5-2020-Bc
17 | 2 | Acrylic_or_Polycarbonate_Left_Front_Back_Cover
18 | 3 | HFS5-2020-300
19 | 1 | HFS5-2020-300
20 | 2 | HFS5-2020-569.5
21 | 2 | HFS5-2020-567.5
22 | 2 | HFS5-2020-218
23 | 5 | HSCA5-R_270mm
24 | 1 | HSCA5-R_170mm
25 | 2 | HSCA5-R_569.5mm
26 | 2 | HSCA5-R_537.5mm
27 | 2 | HSCA5-R_218mm
28 | 1 | Acrylic_or_Polycarbonate_Right_Cover
29 | 2 | Acrylic_or_Polycarbonate_SplitTop_Cover
30 | 1 | Acrylic_or_Polycarbonate_Cover_Door

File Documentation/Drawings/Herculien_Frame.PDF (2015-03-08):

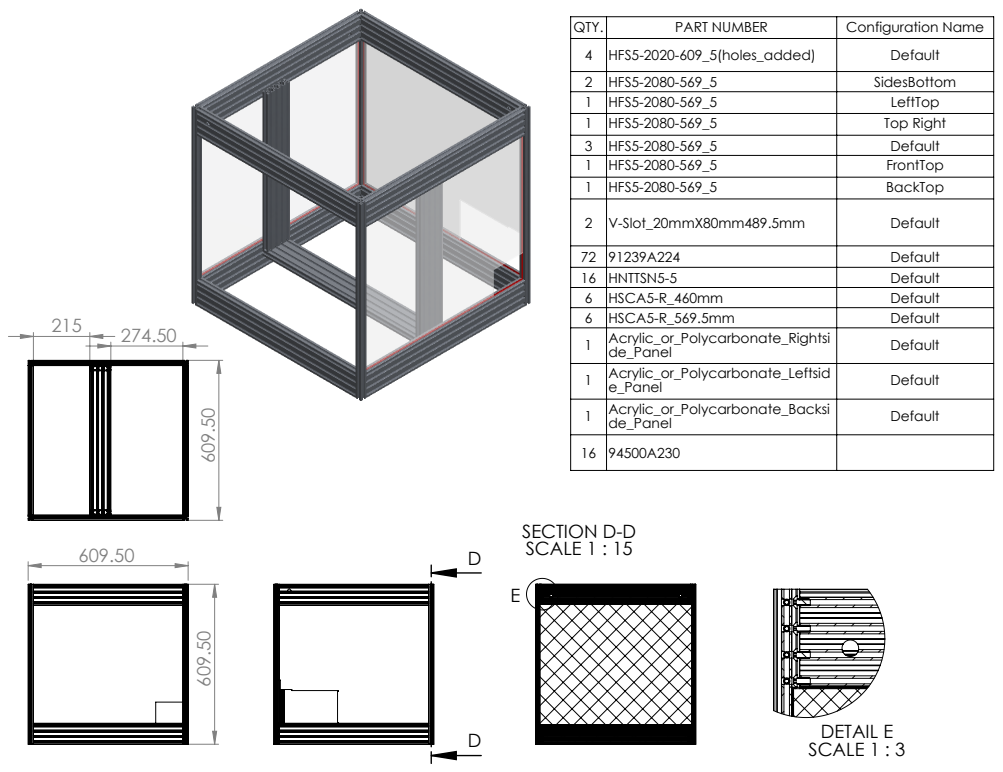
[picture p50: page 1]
SECTION D-D SCALE 1 : 15; DETAIL E SCALE 1 : 3

QTY. | PART NUMBER | Configuration Name
4 | HFS5-2020-609_5(holes_added) | Default
2 | HFS5-2080-569_5 | SidesBottom
1 | HFS5-2080-569_5 | LeftTop
1 | HFS5-2080-569_5 | Top Right
3 | HFS5-2080-569_5 | Default
1 | HFS5-2080-569_5 | FrontTop
1 | HFS5-2080-569_5 | BackTop

2 | V-Slot_20mmX80mm489.5mm | Default
72 | 91239A224 | Default
16 | HNTTSN5-5 | Default
6 | HSCA5-R_460mm | Default
6 | HSCA5-R_569.5mm | Default
1 | Acrylic_or_Polycarbonate_Rightsi de_Panel | Default

1 | Acrylic_or_Polycarbonate_Leftsid e_Panel | Default

1 | Acrylic_or_Polycarbonate_Backsi de_Panel | Default

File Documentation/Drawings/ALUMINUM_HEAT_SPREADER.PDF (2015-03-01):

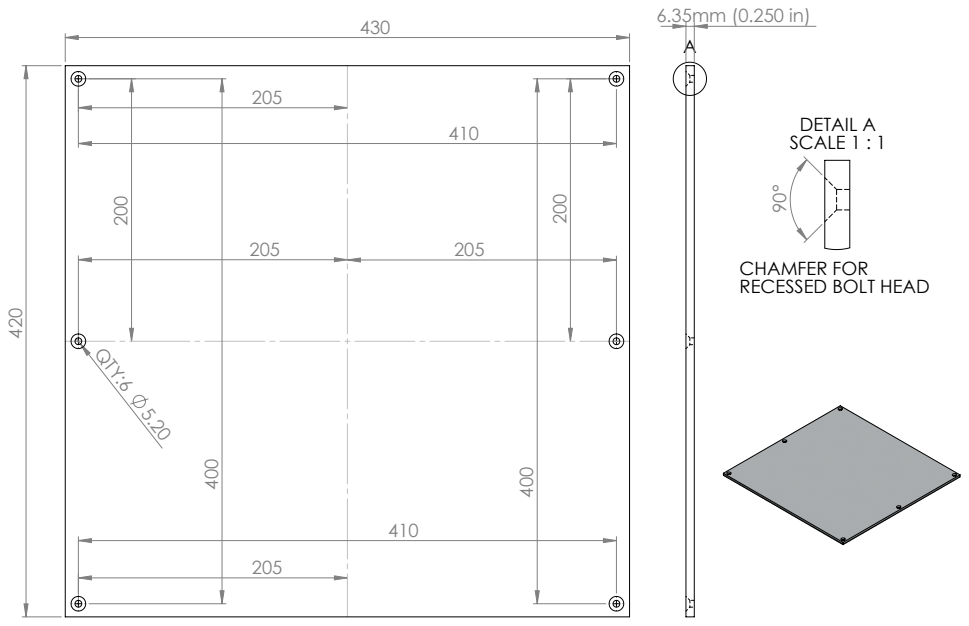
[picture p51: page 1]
DETAIL A SCALE 1 : 1

CHAMFER FOR
RECESSED BOLT HEAD

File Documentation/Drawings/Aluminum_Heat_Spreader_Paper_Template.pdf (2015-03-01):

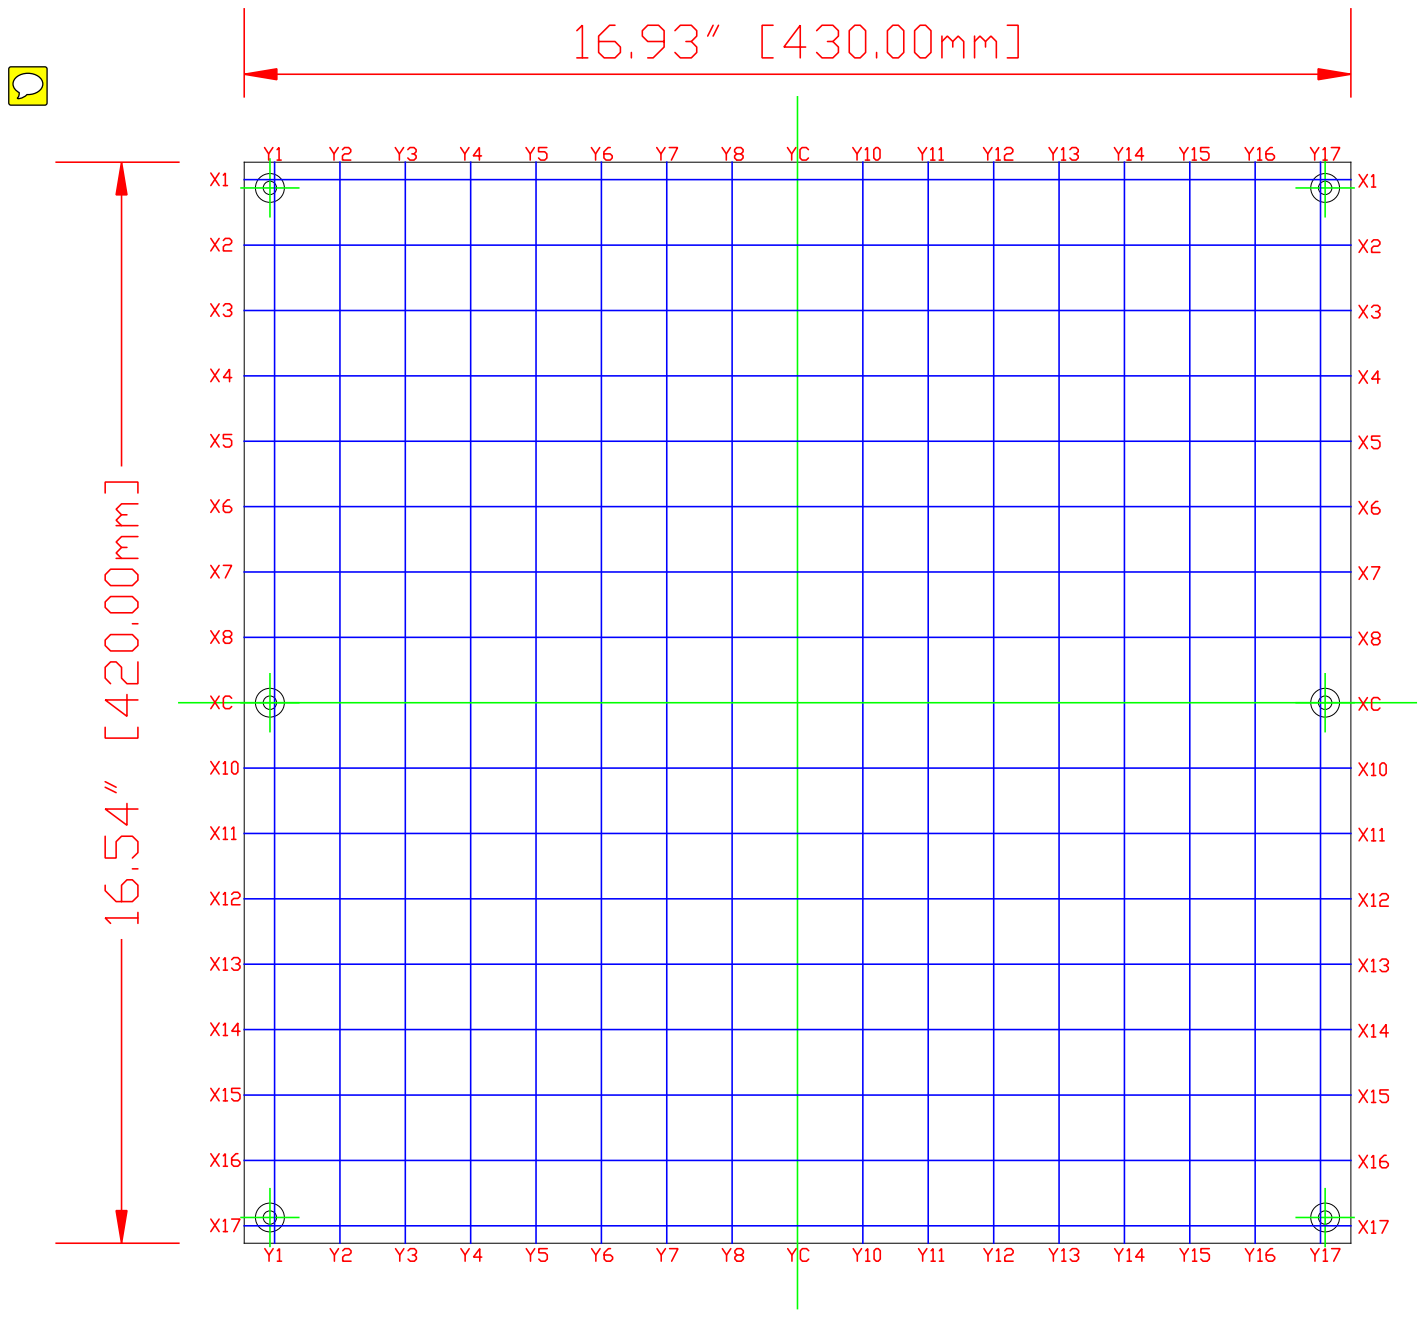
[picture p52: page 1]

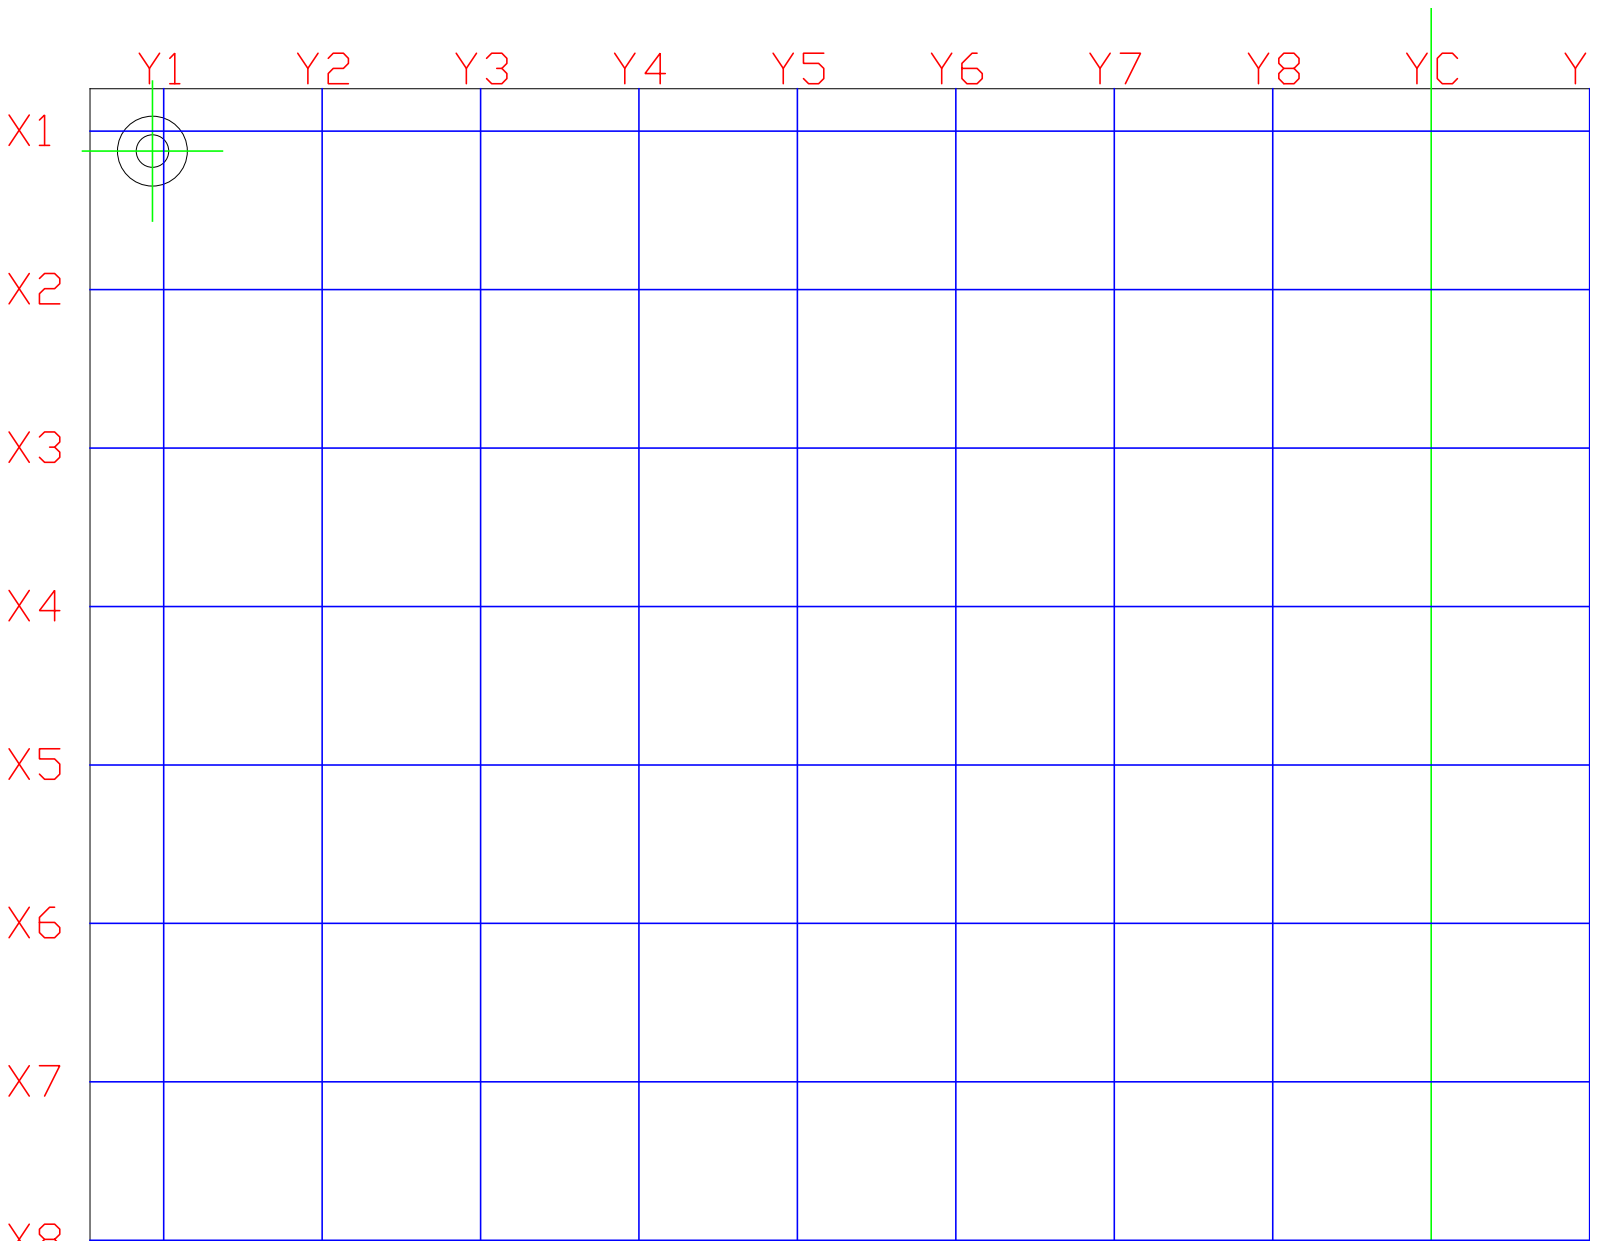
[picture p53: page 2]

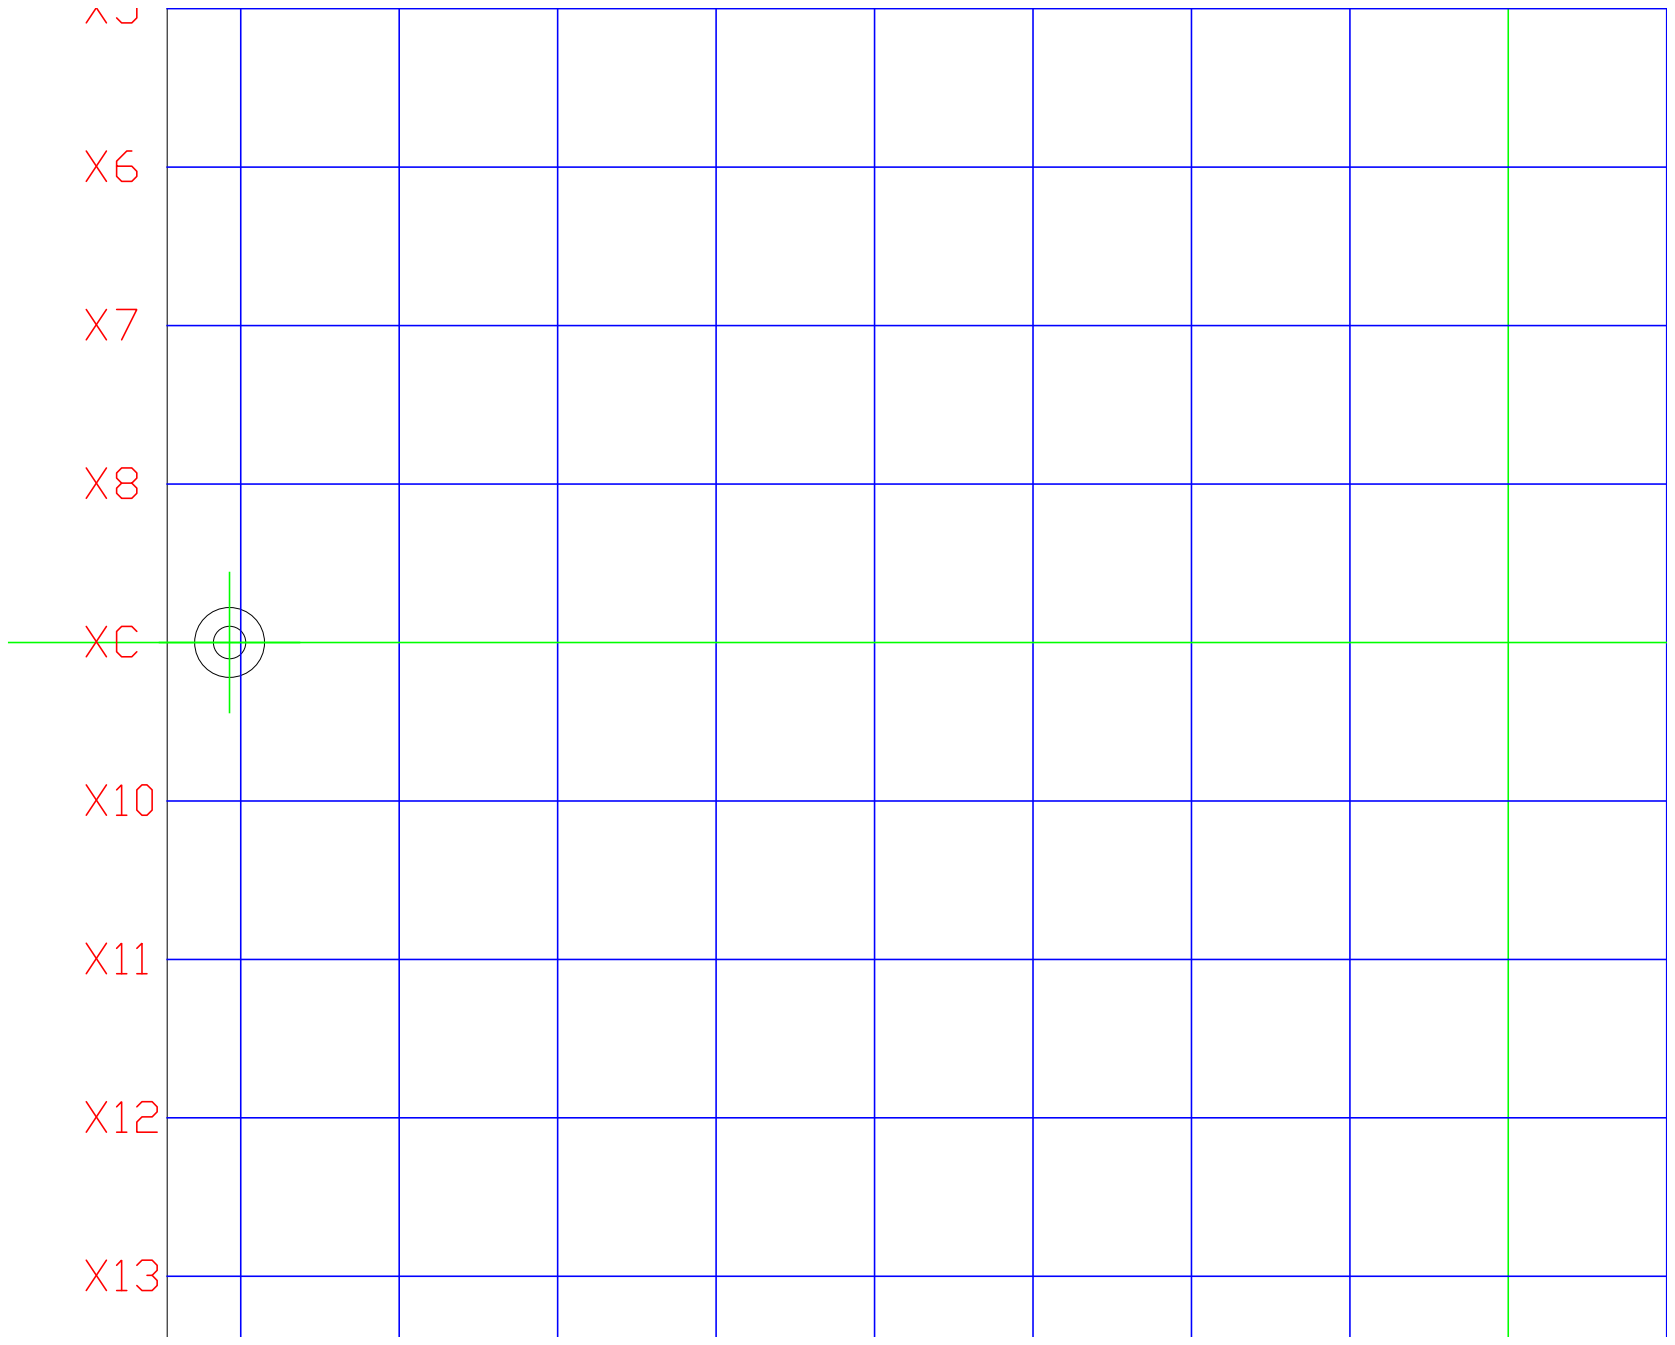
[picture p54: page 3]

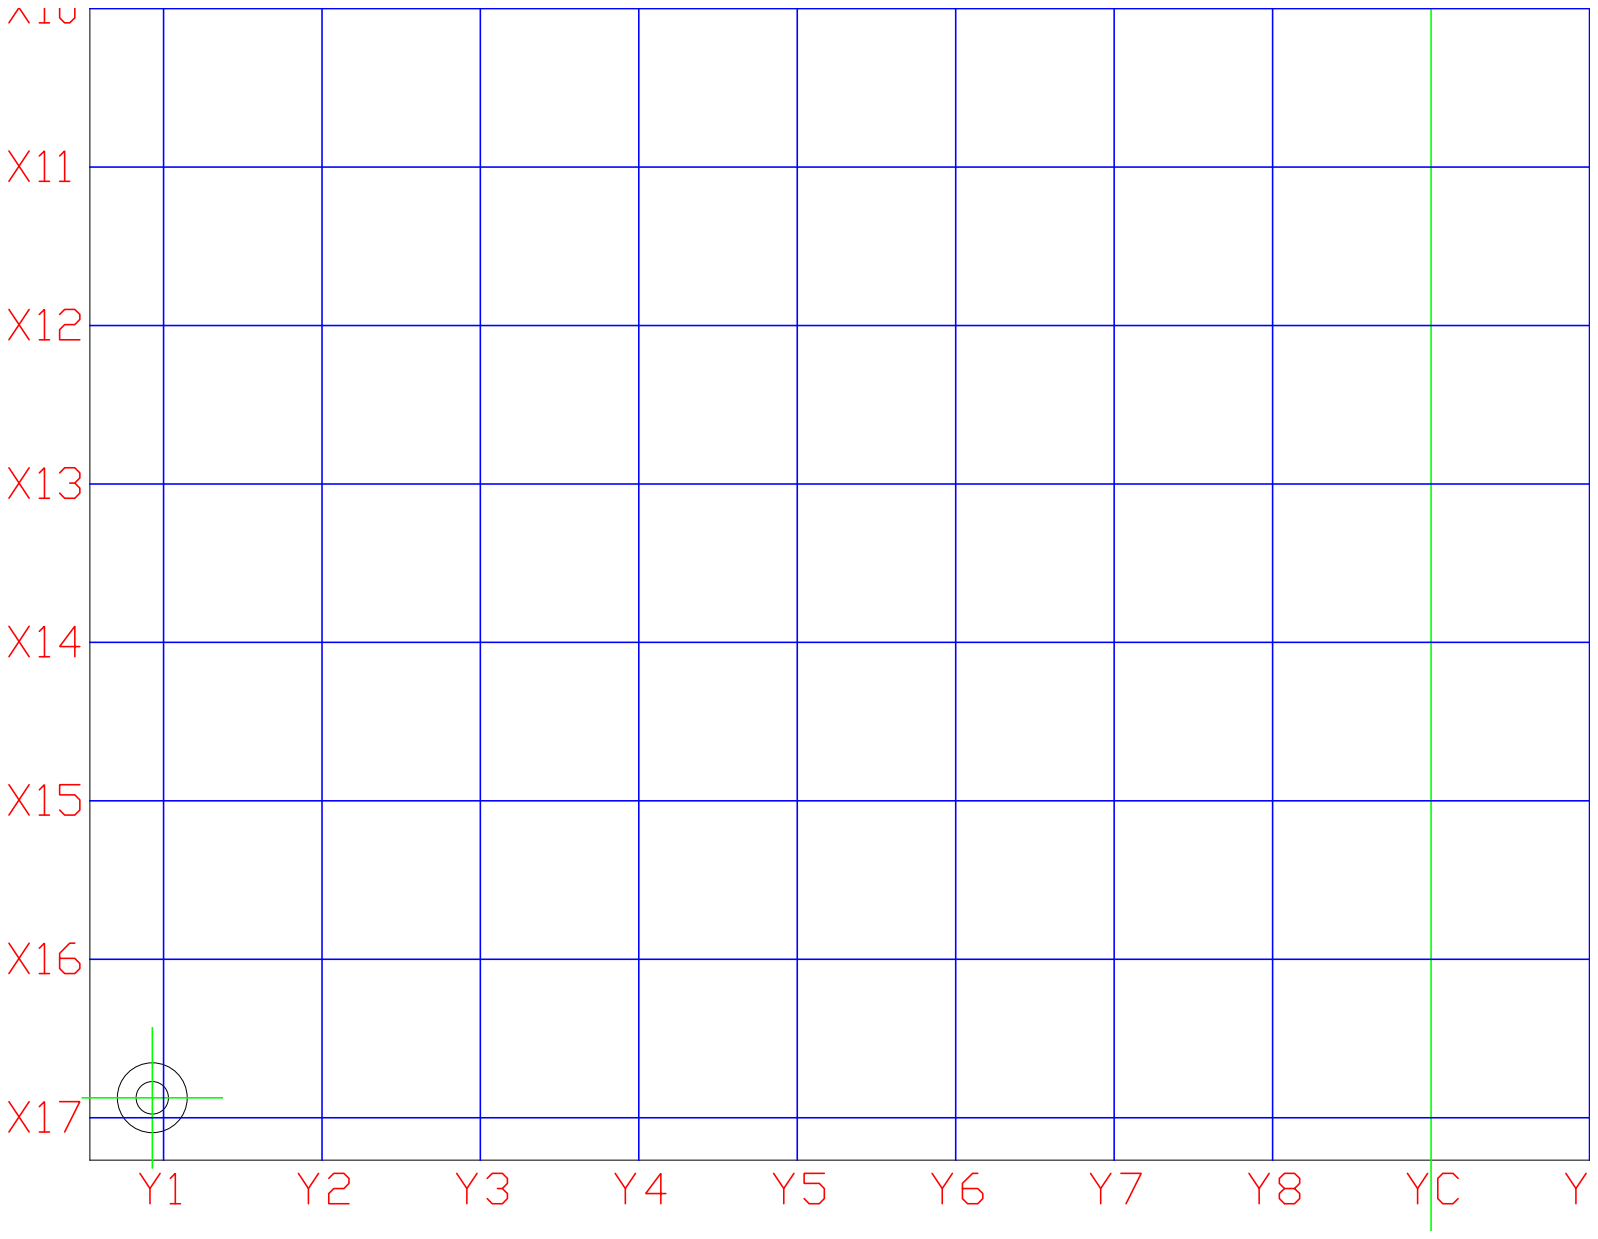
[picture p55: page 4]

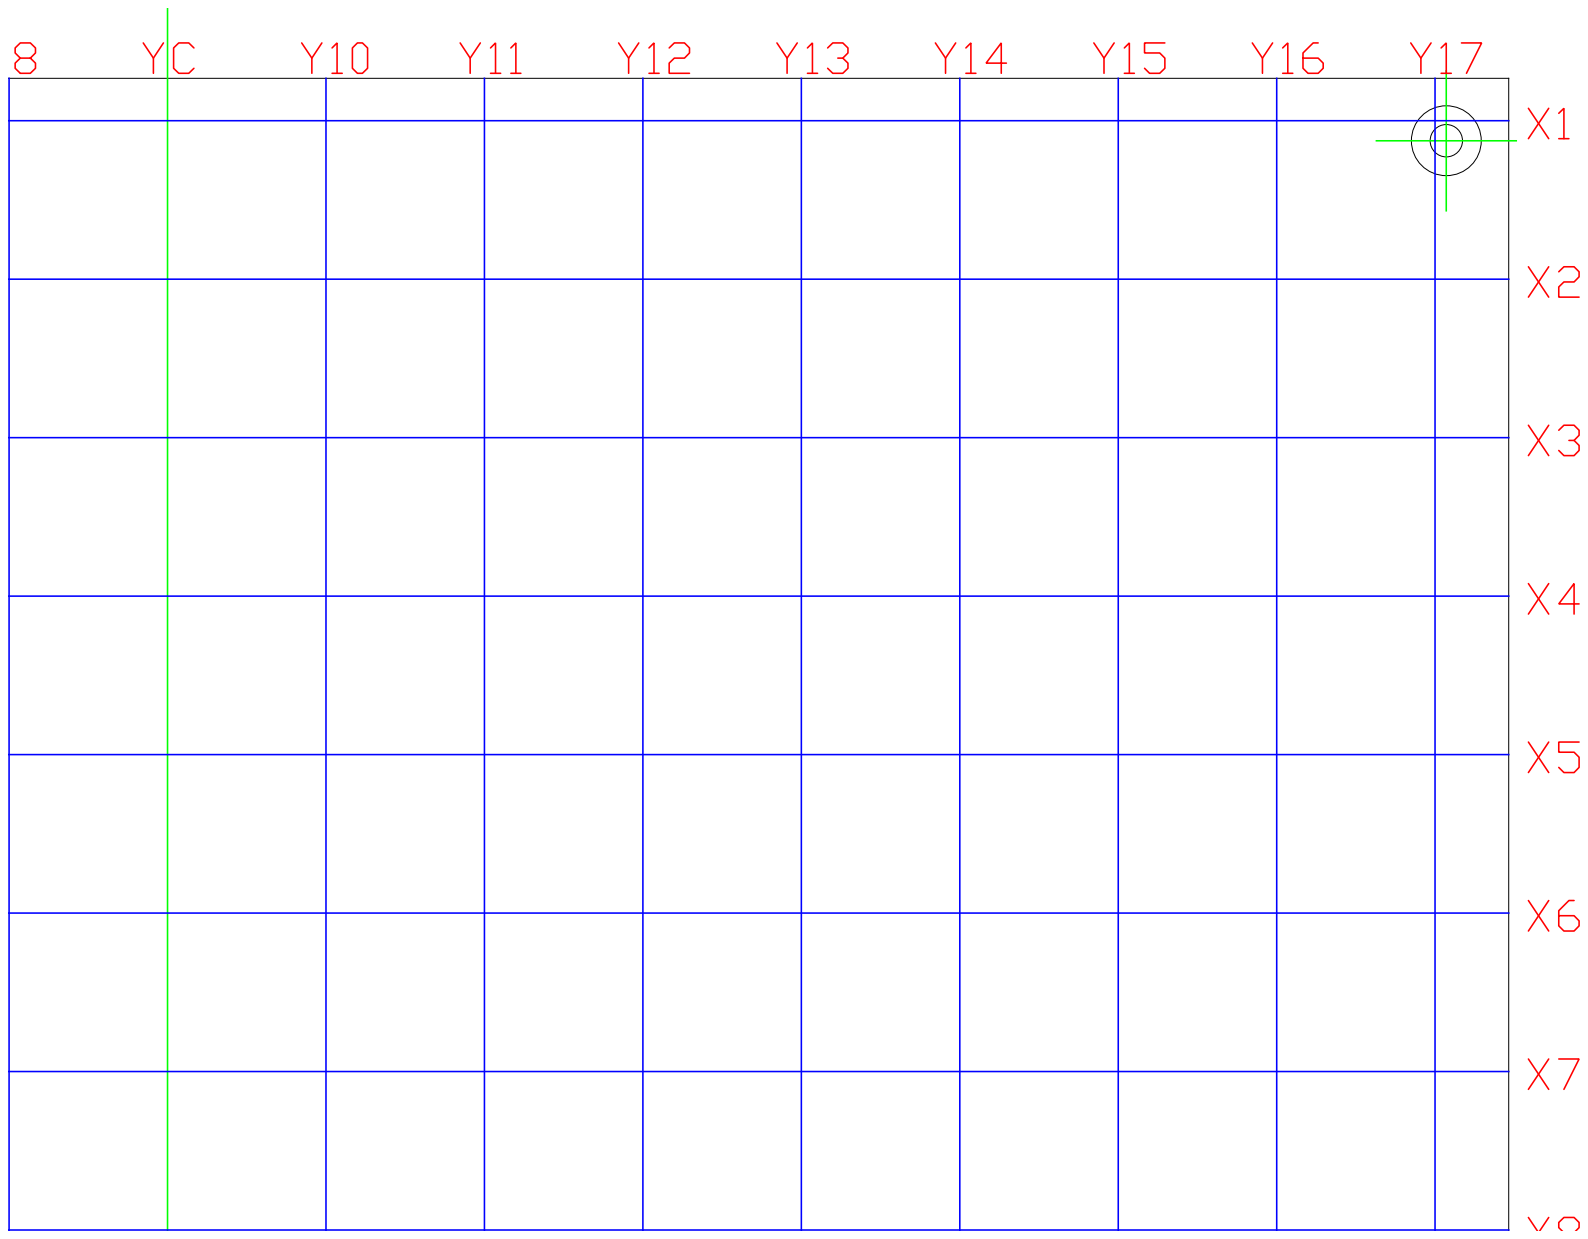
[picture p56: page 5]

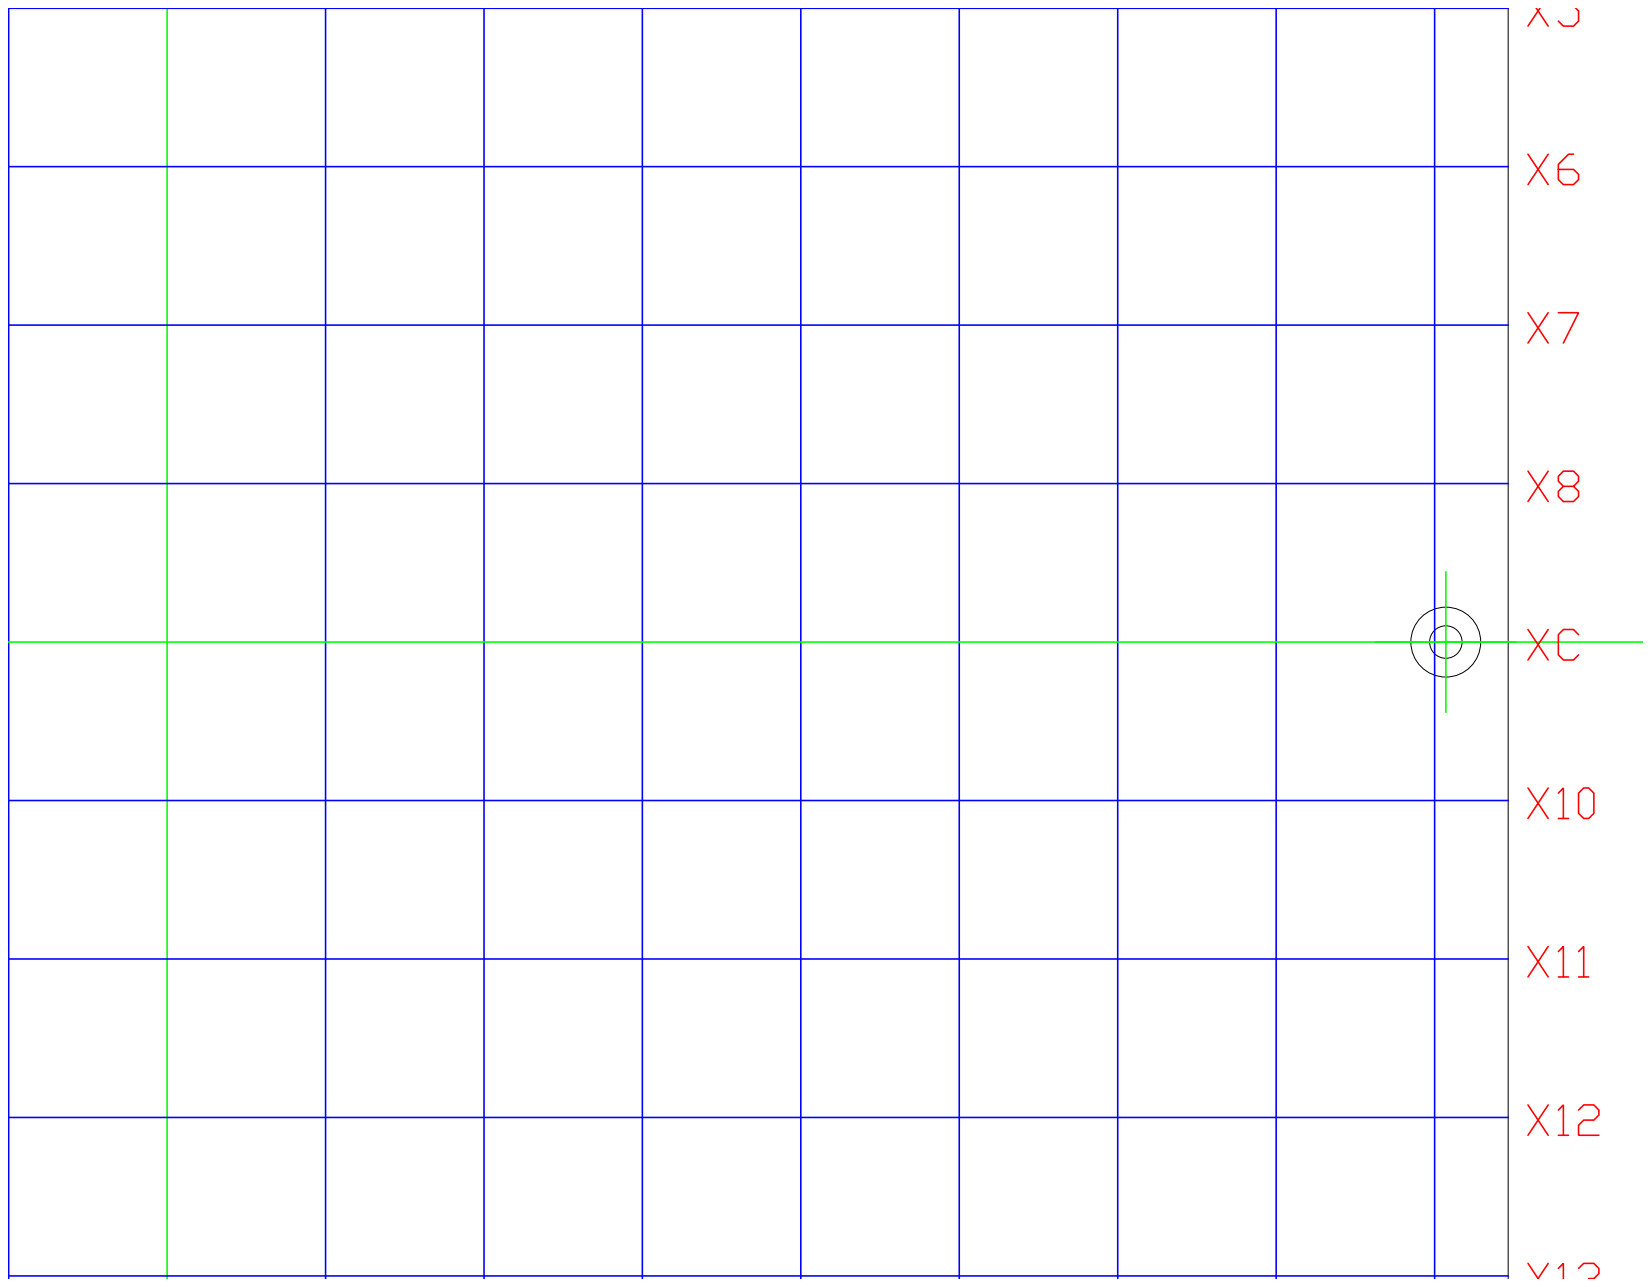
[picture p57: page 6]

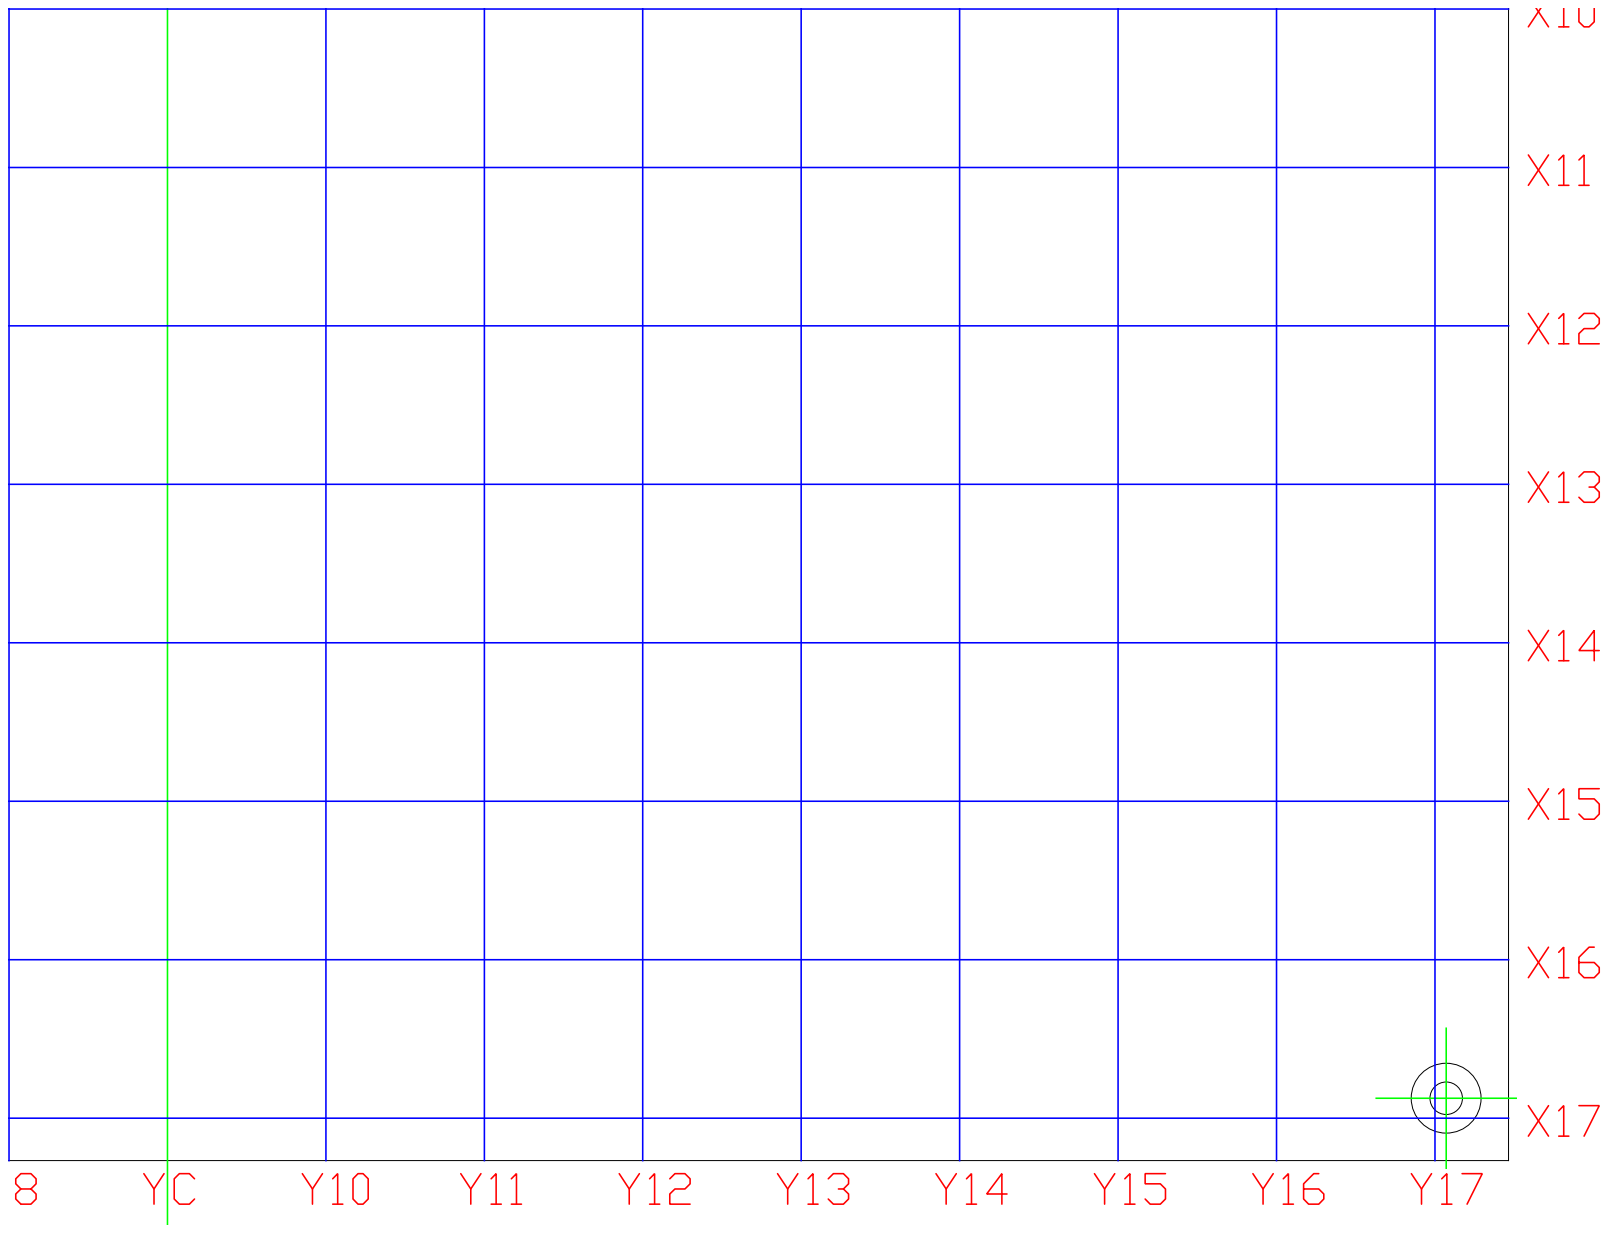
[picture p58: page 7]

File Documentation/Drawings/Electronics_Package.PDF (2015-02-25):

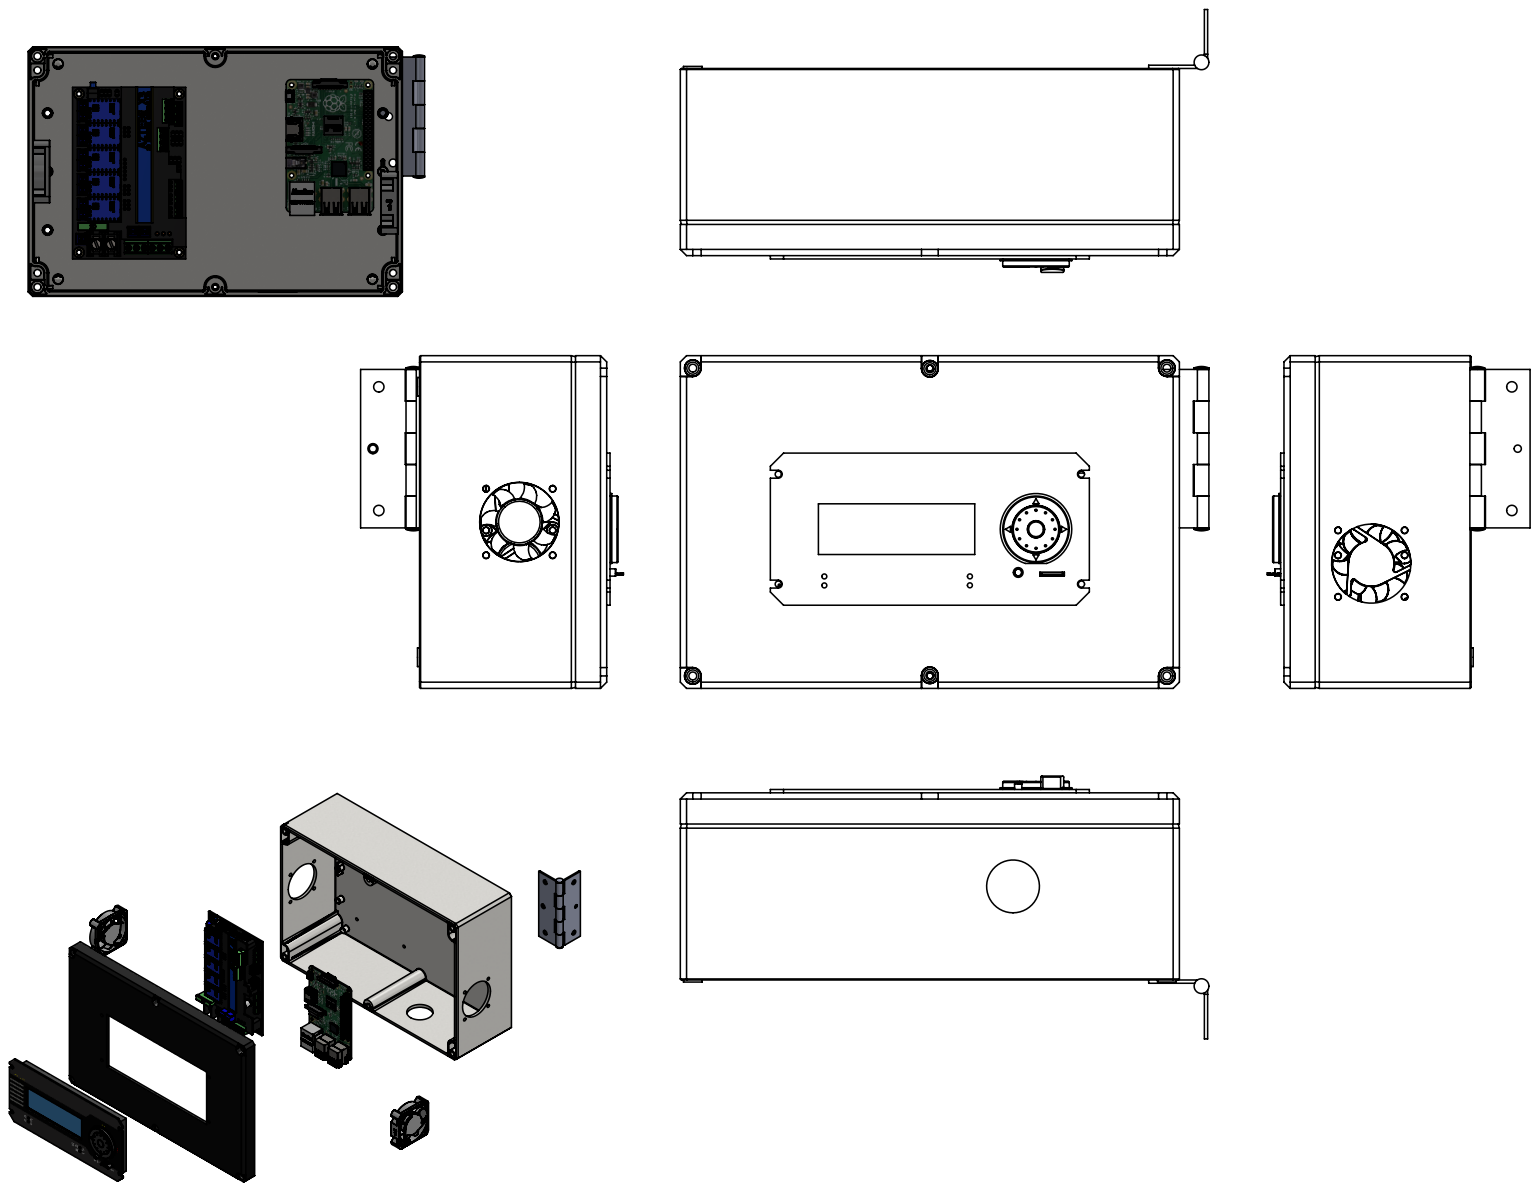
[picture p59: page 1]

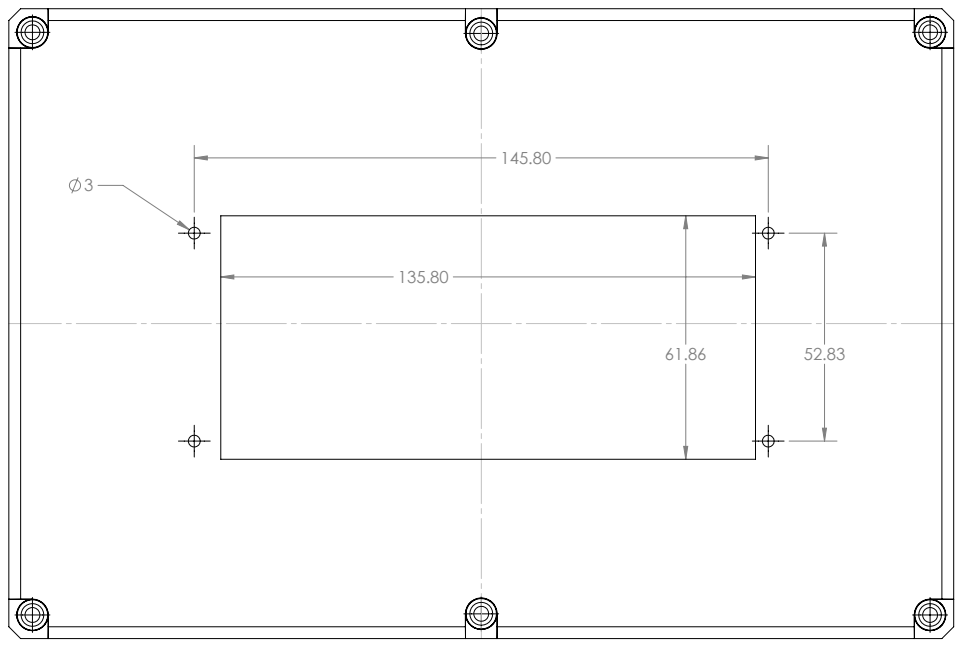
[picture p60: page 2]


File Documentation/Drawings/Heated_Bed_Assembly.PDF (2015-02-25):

DETAIL B SCALE 2 : 5; SECTION C-C SCALE 2 : 5


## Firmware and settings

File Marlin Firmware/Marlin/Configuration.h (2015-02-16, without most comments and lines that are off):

#define CONFIGURATION_H
#define STRING_VERSION_CONFIG_H __DATE__ " " __TIME__ // build date and time
#define STRING_CONFIG_H_AUTHOR "(Eric Lien, Lien3D_HercuLien)" // Who made the changes.
#define SERIAL_PORT 0
#define BAUDRATE 115200
#define MOTHERBOARD 67
#define CUSTOM_MENDEL_NAME "HercuLien"
#define EXTRUDERS 2
#define POWER_SUPPLY 1
#define TEMP_SENSOR_0 1
#define TEMP_SENSOR_1 1
#define TEMP_SENSOR_BED 60
#define MAX_REDUNDANT_TEMP_SENSOR_DIFF 10
#define TEMP_RESIDENCY_TIME 10  // (seconds)
#define TEMP_HYSTERESIS 3       // (degC) range of +/- temperatures considered "close" to the target one
#define TEMP_WINDOW     1       // (degC) Window around target to start the residency timer x degC early.
#define HEATER_0_MINTEMP 5
#define HEATER_1_MINTEMP 5
#define BED_MINTEMP 5
#define HEATER_0_MAXTEMP 285
#define HEATER_1_MAXTEMP 285
#define BED_MAXTEMP 160
#define PIDTEMP
#define BANG_MAX 255 // limits current to nozzle while in bang-bang mode; 255=full current
#define PID_MAX 255 // limits current to nozzle while PID is active (see PID_FUNCTIONAL_RANGE below); 255=full current
  #define PID_FUNCTIONAL_RANGE 10 // If the temperature difference between the target temperature and the actual temperature
  #define PID_INTEGRAL_DRIVE_MAX 255  //limit for the integral term
  #define K1 0.95 //smoothing factor within the PID
  #define PID_dT ((OVERSAMPLENR * 8.0)/(F_CPU / 64.0 / 256.0)) //sampling period of the temperature routine
    #define  DEFAULT_Kp 12.18
    #define  DEFAULT_Ki 0.71
    #define  DEFAULT_Kd 52.09
#define PIDTEMPBED
#define MAX_BED_POWER 220 // limits duty cycle to bed; 255=full current
    #define  DEFAULT_bedKp 213.10
    #define  DEFAULT_bedKi 40.64
    #define  DEFAULT_bedKd 279.32
#define PREVENT_DANGEROUS_EXTRUDE
#define EXTRUDE_MINTEMP 150
#define EXTRUDE_MAXLENGTH 1000 //prevent extrusion of very large distances.
#define THERMAL_RUNAWAY_PROTECTION_PERIOD 60 //in seconds
#define THERMAL_RUNAWAY_PROTECTION_HYSTERESIS 6 // in degree Celsius
#define THERMAL_RUNAWAY_PROTECTION_BED_PERIOD 40 //in seconds
#define THERMAL_RUNAWAY_PROTECTION_BED_HYSTERESIS 4 // in degree Celsius
#define ENDSTOPPULLUPS // Comment this out (using // at the start of the line) to disable the endstop pullup resistors
  #define ENDSTOPPULLUP_XMAX
  #define ENDSTOPPULLUP_YMAX
  #define ENDSTOPPULLUP_ZMAX
  #define ENDSTOPPULLUP_XMIN
  #define ENDSTOPPULLUP_YMIN
  #define ENDSTOPPULLUP_ZMIN
const bool X_MIN_ENDSTOP_INVERTING = true; // set to true to invert the logic of the endstop.
const bool Y_MIN_ENDSTOP_INVERTING = true; // set to true to invert the logic of the endstop.
const bool Z_MIN_ENDSTOP_INVERTING = true; // set to true to invert the logic of the endstop.
const bool X_MAX_ENDSTOP_INVERTING = true; // set to true to invert the logic of the endstop.
const bool Y_MAX_ENDSTOP_INVERTING = true; // set to true to invert the logic of the endstop.
const bool Z_MAX_ENDSTOP_INVERTING = true; // set to true to invert the logic of the endstop.
#if defined(COREXY) && !defined(DISABLE_MAX_ENDSTOPS)
  #define DISABLE_MAX_ENDSTOPS
#endif
#define X_ENABLE_ON 0
#define Y_ENABLE_ON 0
#define Z_ENABLE_ON 0
#define E_ENABLE_ON 0 // For all extruders
#define DISABLE_X false
#define DISABLE_Y false
#define DISABLE_Z false
#define DISABLE_E false // For all extruders
#define DISABLE_INACTIVE_EXTRUDER true //disable only inactive extruders and keep active extruder enabled
#define INVERT_X_DIR true    // for Mendel set to false, for Orca set to true
#define INVERT_Y_DIR false    // for Mendel set to true, for Orca set to false
#define INVERT_Z_DIR false     // for Mendel set to false, for Orca set to true
#define INVERT_E0_DIR false   // for direct drive extruder v9 set to true, for geared extruder set to false
#define INVERT_E1_DIR false    // for direct drive extruder v9 set to true, for geared extruder set to false
#define X_HOME_DIR -1
#define Y_HOME_DIR -1
#define Z_HOME_DIR -1
#define min_software_endstops true // If true, axis won't move to coordinates less than HOME_POS.
#define max_software_endstops true  // If true, axis won't move to coordinates greater than the defined lengths below.
#define X_MAX_POS 338
#define X_MIN_POS 0
#define Y_MAX_POS 358
#define Y_MIN_POS 0
#define Z_MAX_POS 320
#define Z_MIN_POS 0
#define X_MAX_LENGTH (X_MAX_POS - X_MIN_POS)
#define Y_MAX_LENGTH (Y_MAX_POS - Y_MIN_POS)
#define Z_MAX_LENGTH (Z_MAX_POS - Z_MIN_POS)
#define MANUAL_X_HOME_POS 0
#define MANUAL_Y_HOME_POS 0
#define MANUAL_Z_HOME_POS 0
#define NUM_AXIS 4 // The axis order in all axis related arrays is X, Y, Z, E
#define HOMING_FEEDRATE {70*60, 70*60, 12*60, 0}  // set the homing speeds (mm/min)
#define DEFAULT_AXIS_STEPS_PER_UNIT   {80,80,2880,486}  // default steps per unit for Ultimaker (Hercustruder = 580, Bondtech BETA 1 = 486)
#define DEFAULT_MAX_FEEDRATE          {400, 400, 12, 45}    // (mm/sec)
#define DEFAULT_MAX_ACCELERATION      {9000,9000,80,10000}    // X, Y, Z, E maximum start speed for accelerated moves. E default values are good for Skeinforge 40+, for older versions raise them a lot.
#define DEFAULT_ACCELERATION          4000    // X, Y, Z and E max acceleration in mm/s^2 for printing moves
#define DEFAULT_RETRACT_ACCELERATION  4000   // X, Y, Z and E max acceleration in mm/s^2 for retracts
#define DEFAULT_XYJERK                20.0    // (mm/sec)
#define DEFAULT_ZJERK                 0.4     // (mm/sec)
#define DEFAULT_EJERK                 5.0    // (mm/sec)
#define CUSTOM_M_CODES
  #define CUSTOM_M_CODE_SET_Z_PROBE_OFFSET 851
  #define Z_PROBE_OFFSET_RANGE_MIN -15
  #define Z_PROBE_OFFSET_RANGE_MAX -5
#define EEPROM_SETTINGS
#define PLA_PREHEAT_HOTEND_TEMP 180
#define PLA_PREHEAT_HPB_TEMP 70
#define PLA_PREHEAT_FAN_SPEED 255   // Insert Value between 0 and 255
#define ABS_PREHEAT_HOTEND_TEMP 230
#define ABS_PREHEAT_HPB_TEMP 110
#define ABS_PREHEAT_FAN_SPEED 255   // Insert Value between 0 and 255
#define SDSUPPORT // Enable SD Card Support in Hardware Console
#define LCD_I2C_VIKI
  #define LCD_I2C_TYPE_MCP23017
  #define LCD_I2C_ADDRESS 0x20 // I2C Address of the port expander
  #define LCD_USE_I2C_BUZZER //comment out to disable buzzer on LCD (requires LiquidTWI2 v1.2.3 or later)
  #define NEWPANEL
  #define ULTIPANEL
  #define SDSUPPORT
  #define ULTRA_LCD
    #define LCD_WIDTH 20
    #define LCD_HEIGHT 4
#define SOFT_PWM_SCALE 0
#include "Configuration_adv.h"
#include "thermistortables.h"

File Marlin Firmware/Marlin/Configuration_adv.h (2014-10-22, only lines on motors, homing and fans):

#define CONTROLLERFAN_PIN -1 //Pin used for the fan to cool controller (-1 to disable)
#define EXTRUDER_0_AUTO_FAN_PIN   16
#define EXTRUDER_1_AUTO_FAN_PIN   16
#define ENDSTOPS_ONLY_FOR_HOMING // If defined the endstops will only be used for homing
#define X_HOME_RETRACT_MM 5
#define Y_HOME_RETRACT_MM 5
#define Z_HOME_RETRACT_MM 2
#define MICROSTEP1 LOW,LOW
#define MICROSTEP2 HIGH,LOW
#define MICROSTEP4 LOW,HIGH
#define MICROSTEP8 HIGH,HIGH
#define MICROSTEP16 HIGH,HIGH
#define MICROSTEP_MODES {16,16,16,16,16} // [1,2,4,8,16]
#define DIGIPOT_MOTOR_CURRENT {135,135,135,135,135} // Values 0-255 (RAMBO 135 = ~0.75A, 185 = ~1A)
#define DIGIPOT_I2C_MOTOR_CURRENTS {1.0, 1.0, 1.0, 1.0, 1.0, 1.0, 1.0, 1.0}

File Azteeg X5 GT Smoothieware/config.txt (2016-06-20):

# Robot module configurations : general handling of movement G-codes and slicing into moves
default_feed_rate                            12000             # Default rate ( mm/minute ) for G1/G2/G3 moves
default_seek_rate                            12000             # Default rate ( mm/minute ) for G0 moves
mm_per_arc_segment                           0.5              # Arcs are cut into segments ( lines ), this is the length for these segments.  Smaller values mean more resolution, higher values mean faster computation
#mm_per_line_segment                          5                # Lines can be cut into segments ( not usefull with cartesian coordinates robots ).

# Arm solution configuration : Cartesian robot. Translates mm positions into stepper positions
alpha_steps_per_mm                           160               # Steps per mm for alpha stepper
beta_steps_per_mm                            160               # Steps per mm for beta stepper
gamma_steps_per_mm                           2880       # Steps per mm for gamma stepper 1637.7953

# Planner module configuration : Look-ahead and acceleration configuration
planner_queue_size                           32               # DO NOT CHANGE THIS UNLESS YOU KNOW EXACTLY WHAT YOUR ARE DOING
acceleration                                 3000             # Acceleration in mm/second/second.
z_acceleration                               300              # Acceleration for Z only moves in mm/s^2, 0 disables it, disabled by default. DO NOT SET ON A DELTA
acceleration_ticks_per_second                1000             # Number of times per second the speed is updated
junction_deviation                           0.05             # Similar to the old "max_jerk", in millimeters, see : https://github.com/grbl/grbl/blob/master/planner.c#L409
                                                              # and https://github.com/grbl/grbl/wiki/Configuring-Grbl-v0.8 . Lower values mean being more careful, higher values means being faster and have more jerk
z_junction_deviation                         0.0

# Stepper module configuration
microseconds_per_step_pulse                  1                # Duration of step pulses to stepper drivers, in microseconds
base_stepping_frequency                      100000           # Base frequency for stepping
# Stepper module pins ( ports, and pin numbers, appending "!" to the number will invert a pin )
alpha_step_pin                               2.1             # Pin for alpha stepper step signal
alpha_dir_pin                                0.11!             # Pin for alpha stepper direction
alpha_en_pin                                 0.10             # Pin for alpha enable pin 0.10
alpha_current                                0.6              # VREF VOLTAGE!! X stepper vref voltage
x_axis_max_speed                             30000            # mm/min
alpha_max_rate                               30000.0          # mm/min actuator max speed

beta_step_pin                                2.2              # Pin for beta stepper step signal
beta_dir_pin                                 0.20             # Pin for beta stepper direction
beta_en_pin                                  0.19             # Pin for beta enable
beta_current                                 0.6              # VREF VOLTAGE!! Y stepper vref voltage
y_axis_max_speed                             30000            # mm/min
beta_max_rate                                30000.0          # mm/min actuator max speed

gamma_step_pin                               2.3              # Pin for gamma stepper step signal
gamma_dir_pin                                0.22!            # Pin for gamma stepper direction
gamma_en_pin                                 0.21             # Pin for gamma enable
gamma_current                                0.6              # VREF VOLTAGE!! Z stepper vref voltage
z_axis_max_speed                             720              # mm/min
gamma_max_rate                               720.0            # mm/min actuator max speed

# Serial communications configuration ( baud rate default to 9600 if undefined )
uart0.baud_rate                              250000           # Baud rate for the default hardware serial port
second_usb_serial_enable                     false            # This enables a second usb serial port (to have both pronterface and a terminal connected)
#msd_disable                                 false            # disable the MSD (USB SDCARD) when set to true


# Extruder module configuration
extruder.hotend.enable                          true             # Whether to activate the extruder module at all. All configuration is ignored if false
extruder.hotend.steps_per_mm                    972              # Steps per mm for extruder stepper
extruder.hotend.default_feed_rate               600              # Default rate ( mm/minute ) for moves where only the extruder moves
extruder.hotend.acceleration                    1000             # Acceleration for the stepper motor mm/sec²
extruder.hotend.max_speed                       80               # mm/s

extruder.hotend.step_pin                        2.0             # Pin for extruder step signal
extruder.hotend.dir_pin                         0.5             # Pin for extruder dir signal
extruder.hotend.en_pin                          0.4             # Pin for extruder enable signal

# extruder offset
extruder.hotend.x_offset                        0                # x offset from origin in mm
extruder.hotend.y_offset                        0                # y offset from origin in mm
extruder.hotend.z_offset                        0                # z offset from origin in mm

# firmware retract settings when using G10/G11, these are the defaults if not defined, must be defined for each extruder if not using the defaults
extruder.hotend.retract_length                  6.5              # retract length in mm
extruder.hotend.retract_feedrate                70               # retract feedrate in mm/sec
extruder.hotend.retract_recover_length          0                # additional length for recover
extruder.hotend.retract_recover_feedrate        65               # recover feedrate in mm/sec (should be less than retract feedrate)
extruder.hotend.retract_zlift_length            .2               # zlift on retract in mm, 0 disables
extruder.hotend.retract_zlift_feedrate          720             # zlift feedrate in mm/min (Note mm/min NOT mm/sec)
delta_current                                    0.5             # VREF VOLTAGE!! Extruder 1 stepper vref voltage.

# Second extruder module configuration
extruder.hotend2.enable                          true             # Whether to activate the extruder module at all. All configuration is ignored if false
extruder.hotend2.steps_per_mm                    972              # Steps per mm for extruder stepper
extruder.hotend2.default_feed_rate               600              # Default rate ( mm/minute ) for moves where only the extruder moves
extruder.hotend2.acceleration                    1000             # Acceleration for the stepper motor, as of 0.6, arbitrary ratio
extruder.hotend2.max_speed                       80               # mm/s

extruder.hotend2.step_pin                        2.8              # Pin for extruder step signal
extruder.hotend2.dir_pin                         2.13             # Pin for extruder dir signal
extruder.hotend2.en_pin                          4.29             # Pin for extruder enable signal

extruder.hotend2.x_offset                        33.3             # x offset from origin in mm
extruder.hotend2.y_offset                        0.5              # y offset from origin in mm
extruder.hotend2.z_offset                        0                # z offset from origin in mm
epsilon_current                                  0.5              # VREF VOLTAGE!! Extruder 2 stepper vref voltage.



# Laser module configuration
laser_module_enable                          false             # Whether to activate the laser module at all. All configuration is ignored if false.
#laser_module_pin                             2.7              # this pin will be PWMed to control the laser
#laser_module_max_power                       0.8              # this is the maximum duty cycle that will be applied to the laser
#laser_module_tickle_power                    0.0              # this duty cycle will be used for travel moves to keep the laser active without actually burning
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

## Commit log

2014-09-04 First Upload
    Incomplete Center Carriage Assembly, Complete XY Rod End Carriage
    Assemblies With Belt Tensioners
    [3mmX25mm_Buttonhead(McMaster_91239A126).SLDPRT, 3mmX25mm_Sockethead(McMaster_91290A125).SLDPRT, 3mmX50mm_Sockethead(McMaster_91290A137).SLDPRT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]
2014-10-09 Adding more items and cleaning up models
    Adding more items and cleaning up models
    [12mm_Leadscrew.SLDPRT, 2 Way PCB Screw Terminal Block 2.5mm_Défaut.sldprt, 2 Way PCB Screw Terminal Block 3_5mm.sldprt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]
2014-10-22 Adding Subassemblies to HercuLien Master Assembly
    Beginning adding subassemblies into HercuLien Master Assembly Model.
    [50x50x15_Fonsoning_FSY5015S24H_Blower.SLDPRT, Aluminum_Build_Plate.SLDPRT, Blower_Duct_1.SLDPRT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]
2014-11-03 Dual E3D V6 Carriage, Added New Heated Bed
    Dual E3D V6 Carriage, Added New Heated Bed
    [.75L_.5OD_.062Wire(McMaster_9657K292).SLDPRT, 30x30_Fan.SLDASM, 380mmx380mm_800W_120V_Silicone_Heater(Alirubber).SLDPRT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]
2014-11-07 Add electronics package components and z-belt idlers
    Add electronics package components and z-belt idlers
    [2 Way PCB Screw Terminal Block 2.5mm_Défaut.sldprt, 2 Way PCB Screw Terminal Block 3_5mm.sldprt, 3 Way PCB Screw Terminal Block 2.5mm_Défaut.sldprt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]
2014-11-08 Added front door, additional electronics, etc.
    Added front door, additional electronics, etc.
    [50x50x15_Fonsoning_FSY5015S24H_Blower.SLDPRT, 5mmX10mm_Flathead(McMaster_91294A207).SLDPRT, Acrylic_or_Polycarbonate_Door_Window.SLDPRT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]
2014-11-08 Added Additional 3D Formats, Renders, Cover
    1.) Added several other 3d model formats for people without solidworks.
    Many of the other model formats are in 7zip archives due to github size
    limits.
    2.) Added some Render Shots.
    3.) Added top cover.
    [CAT5 Tooless IDC Keystone Jack.SLDPRT, Carriage_Dual_E3DV6.SLDASM, Front_Door.SLDASM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]
2014-11-09 Added STL files for printing and other changes
    I added STL files for printed components, replaced some of the parts
    with standard components to avoid Solidworks toolbox issues, and other
    minor changes.
    [2 Way PCB Screw Terminal Block 2.5mm_Défaut.sldprt, 2 Way PCB Screw Terminal Block 3_5mm.sldprt, 3 Way PCB Screw Terminal Block 2.5mm_Défaut.sldprt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]
2014-11-12 Added missing hardware & side panels
    Added missing hardware to the E3D V6 carriage design, adjusted the
    hotend fan duct for additional material around the bolt holes, and added
    side and back panels.
    [30x30_Fan.SLDASM, 3mmX16mm_Buttonhead(McMaster_92095A184).SLDPRT, 3mmX18mm_Sockethead(McMaster_91292A029).SLDPRT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]
2014-11-13 Finish Cover with hardware
    Finished Cover including all hardware and panels, handles, hinges, etc.
    [5mmX12mm_Sockethead(McMaster_92290A228).SLDPRT, 5mm_Flatwasher(McMaster_90965A160).SLDPRT, Acrylic_or_Polycarbonate_Left_Front_Back_Cover.SLDPRT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]
2014-11-22 Model Adjustments and Full BOM
    Model Subassembly Adjustments and full Bill Of Materials
    [5mmX8mm_Buttonhead(McMaster_94500A230).SLDPRT, Bed_Glass_Clip.SLDPRT, Bed_Glass_Clip.STL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]
2014-11-23 Wrong STL Model Correction
    I had the wrong name on a model for the 50mm round spool holder. This
    corrects that issue.
    [50mm_Threaded_Spool_Holder_Full_Round.STL]
2014-11-23 Updated Other Model Formats
    Updated the exported "other model formats" to the latest revision.
    Renamed a few items for clarity. Updated A Few Drawings.
    [Carriage_Dual_E3DV6.SLDDRW, Dual_Bowden_Tube_Carriage_Adapter.SLDPRT, Dual_Bowden_Tube_Carriage_Adapter.STL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]
2014-11-23 Fixed Broken BOM STL Links
    Fixed Broken BOM STL Links after parts were renamed.
    [HercuLien_BOM.xls]
2015-02-03 Adding drill guide stls and hatchbox filament compatible spool holders. Thanks Eric
    [32mm_Non-Bearing_Spool_Hub.stl, 32mm_Non-Bearing_Spool_HubV2.stl, Extrusion_Drill_Guide.stl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]
2015-02-09 Drawings, Cable Chain, Z ES Trip Arm, Drill Guides
    Drawings, Cable Chain, Z ES Trip Arm, Drill Guides, Printed Hinges
    (optional instead of Misumi ones)
    [0.25x2.5in_Dowel_Pin(McMaster_97395A499).SLDPRT, 2020_Hinge.SLDPRT, Aluminum_Build_Plate.DXF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]
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2015-02-16 Corrections to BOM Links & Drawings
    Corrected some BOM items, added missing 10mm ID shims for where pulleys
    meet the corner bearings (to avoid rub), increased enclosure panels to
    0.177in thick to help with vibration noise, added some dxf drawings of
    panels for CNC or laser cutting, minor marlin firmware tweaks, etc.
    [Acrylic_or_Polycarbonate_Backside_Panel.DXF, Acrylic_or_Polycarbonate_Backside_Panel.SLDPRT, Acrylic_or_Polycarbonate_Door_Window.DXF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]
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2015-02-24 BOM tweaks, drawings, and misc parts
    Changed default belt vendor to Robotdigg for x/y belts, added print for
    mdf bed insulator, added some simpler clips to hold down the glass,
    shortened the led holder for easier printability for smaller printers
    (300mm long which aligns with standard LED segment lengths), added some
    printable handles.
    [Glass Clip.SLDPRT, Glass Clip.STL, Handle_(Printable).SLDPRT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]
2015-02-25 Added more drawing for electronic package
    Added more drawing for electronic package (using Raspberry Pi B+ and
    Azteeg X3)
    [All_The_Extrusion_Pieces.SLDASM, All_The_Extrusion_Pieces.SLDDRW, Break In Gcode Travel Path.dxf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]
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2015-03-01 Added More Drawings
    Drawings of the heat spreader, and a paper template print of the heat
    spreader to aid in fabrication.
    [ALUMINUM_HEAT_SPREADER.SLDDRW, Aluminum_Build_Plate.dwg]
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2015-03-06 Add Break-in Gcode Files
    Added some break-in gcode files for startup of a new printer to work in
    the bushings abd bearing. I have 2 speed versions (100mm/s and 200mm/s)
    as well as versions with and without z-moves for each speed.
    [BreakInCode_Large_(Path_Visualization).dxf]
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2015-03-08 Added front door to cover, and cleaned up the BOM
    Added front door to cover, and cleaned up the BOM.
    Also other misc changes, that I had held back on while I confirmed they
    were correct.
    [5mmX12mm_Sockethead(McMaster_92290A228).SLDPRT, 5mmX16mm_Buttonhead(McMaster_91239A232).SLDPRT, 5mmX8mm_Flathead(McMaster_91294A207).SLDPRT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]
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2015-12-05 A remix of the XY ends designed for the Eustathios and Herculien reprap printers. Please note this is a work in progress and has not been tested extensively. Perceived benefits include:
    1) The bearings have more freedom (more tolerant of misalignment). Smoother motion before running break in routine.
    2) Uses this bearing from Robotdigg (http://www.robotdigg.com/product/451/Selfgraphite+10*14*30mm+Linear+Bearing) and the design could be adapted for Igus or Simplicity bearings.
    3) Bearings are easy to remove and replace.
    4) Split rod clamp simplifies assembly because you can drop the cross bars in place after the outer rods are inserted.
    [151007 - XY end rod clamp - 3DPV rev A.stl, 151007 - XY end snap bearing - 3DPV rev A.stl, 151007 - XY end snap bearing - 3DPV rev A.stp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]
2016-02-24 Add link to ball screw from Golmart
    Thanks to Jim Stone for getting this PN setup with Golmart. The prices are cheaper than Misumi and the ball screw can travel faster. Please note the pitch is different so the steps/mm will need to be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
    [HercuLien_BOM.xls]
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2016-06-12 Zbaird mods 1
    added alternate belt tensioners, v6/volcano carriage, and Z-axis cable
    management
    [Bushing_tool.SLDPRT, Bushing_tool.STL, EZ_belt_tensioner_block_A.SLDPRT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]
2016-06-20 Azteeg X5 GT Config
    Added a few small parts and the config file for the Azteeg X5 GT
    (currently unreleased board as of 06-19-16, but might be released as
    soon as July per Roy).
    [Bed_Glass_Clip(Glass_Plus_PEI).SLDPRT, Bed_Glass_Clip(Glass_Plus_PEI).STL, config.txt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]
2016-06-20 Update to EZ belt tensioners
    Corrected timing belt alignment for belt tensioners, added modified
    limit switch mounts, added break-in gcode with arc movements for more
    comprehensive break-in
    [EZ_belt_tensioner_block_A.SLDPRT, Endstop_mount_EZgantry.SLDPRT, Xmax_Ymin_Endstop_mount_EZgantry.stl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]
2016-08-30 Zane mods repaired and added my dual Bondtech mount
    The amazing mods by Zane were for some reason corrupt when I first
    uploaded them. This should repair that. I also included my dual Bondtech
    mount. The mount requires support to print.
    [Bondtech_DoubleMount.SLDPRT, Bondtech_DoubleMount.STEP, Bondtech_DoubleMount.stl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]
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2016-08-31 A few updated pictures and the Viki2 Mount
    I included a few newer photos of the printer (other pictures are from
    before I upgraded the cover and added Bondtech extruders). I also
    included the Viki2 mount which is part of my upgrade to the Azteeg X5 GT
    controller. This required I remove the hinged front controller box since
    the X5 GT was too big to fit into the hinged box. That's ok, I think the
    new look is cleaner anyway.
    [HercuLien_Viki2_Mount_Front_Face.SLDPRT, HercuLien_Viki2_Mount_Front_Face.STEP, HercuLien_Viki2_Mount_Front_Face.STL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]
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2020-06-16 Add Missing File
    Add Missing File
    [molex_microfit_female_containment.SLDPRT]
